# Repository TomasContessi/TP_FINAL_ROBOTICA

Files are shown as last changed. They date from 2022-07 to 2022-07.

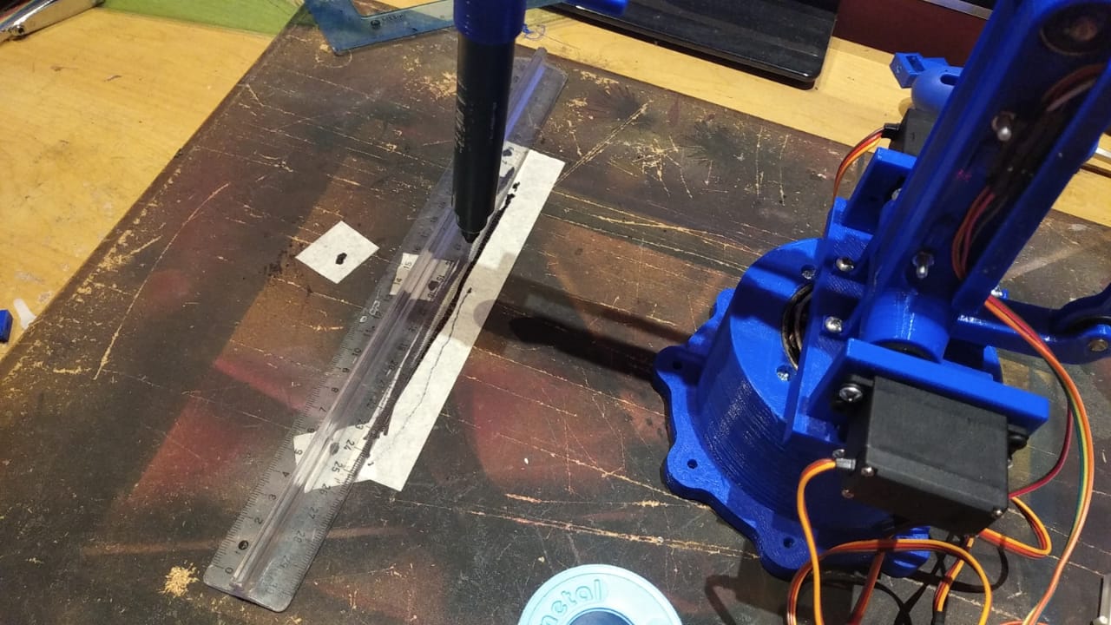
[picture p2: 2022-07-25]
robot irl/img/lineal.jpeg

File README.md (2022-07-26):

# TP FINAL ROBOTICA

Robot serie de 4 grados de libertad fabricado como tp final de la materia robotica.

precision

Especificaciones de diseño:

- Carga Maxima 400g
- Maxima extencion 250mm
- Repetitividad +-1mm
- Exactitud +-1mm
- Peso 1kg

Especificaciones del robot medidas en el prototipo final:

- Carga Maxima 200g
- Maxima extencion 250mm
- Repetitividad +-3mm
- Exactitud +-5mm
- Peso 934g

# Videos del robot

https://user-images.githubusercontent.com/55562600/180897072-30f60ed5-107a-4d38-ac05-319fecedbc43.mp4

https://user-images.githubusercontent.com/55562600/180897452-3dd9bf58-14a9-4827-a617-9365f39d61e9.mp4

https://user-images.githubusercontent.com/55562600/180897461-f654ef13-cb58-4b30-b609-2cc938e993c4.mp4

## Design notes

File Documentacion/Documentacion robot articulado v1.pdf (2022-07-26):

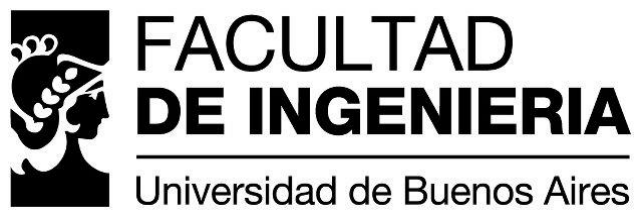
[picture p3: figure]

# Robótica

# Trabajo práctico FINAL-ROBOT

Nombre | Correo Electrónico
Tomas contessi | tcontessi@fi.uba.ar

# Índice:

- Descripción del proyecto.
- Especificaciones deseadas.
- Elección de componentes.
- Diseño de partes mecánicas.
- Simulación y obtención de modelos.
- Revisión de las especificaciones.
- Construcción del prototipo.
- Diseño e implementación del software.
- Pruebas sobre el prototipo y verificación de las especificaciones deseadas.
- Lista de componentes.
- Cosas por mejorar.

# Descripción del proyecto:

Se desea construir un modelo de robot serie de 4 grados de libertad capaz de realizar tareas del tipo pick and place.
Si bien existen modelos de robot y controladores de este estilo en internet, en este proyecto se diseñarán e implementarán tanto el hardware como el software necesario. Los modelos y el software resultantes serán subidos a un repositorio de GitHub para que cualquiera que lo desee pueda acceder a ellos y continuar el desarrollo o construir su prototipo.

Este proyecto utiliza Solid Works para el diseño de piezas mecánicas, simulación y obtención de características físicas, Arduino como plataforma de desarrollo para hacer de interfaz entre la pc y los motores y Python como lenguaje de programación para el controlador.

# Especificaciones deseadas:

Se desea que el prototipo de robot cumpla las siguientes especificaciones:

- Grados de libertad: 4.
- Máxima extensión: 250mm.
- Carga máxima en la brida a máxima extensión: 400g.
- Precisión: ±1mm.
- Repetitividad: ±1mm.
- Velocidad: 100º/seg.
- Peso del robot: 1kg.
- No se pondrán frenos mecánicos, solo los motores.

# Elección de componentes:

Para la construcción del modelo se eligieron los componentes siguiendo un criterio de precio/calidad y simplicidad, eligiéndose los siguientes:

- Motor para los ejes 1,2,3: servomotor Mg946r.
- Motor para el eje 4: servomotor Sg90.
- Placa de desarrollo: Arduino Nano.
- Rodamientos: rulemanes 6262RS
- Rodamiento eje 1: rulemán 30202JR o 30305JR (se utilizó este en el modelo fabricado).
- Material de fabricación de las partes: PLA.

# Diseño de las partes mecánicas:

El diseño del robot tomo inspiración de modelos como el IRB460 de ABB, ya que ese tipo de diseño maximiza la carga útil al poner los motores montados sobre el eje 1 y da la posibilidad de utilizar solo ejes giratorios, a diferencia de modelos como el SCARA. Aunque también tiene la contra de que es un diseño mecánicamente complejo, teniendo los motores de los ejes 2 y 3 montados de manera concéntrica y haciendo uso de un sistema de trapecios (en mi diseño se cambió por romboides) que garantiza que el eje de la brida siempre se mantenga paralelo al suelo.

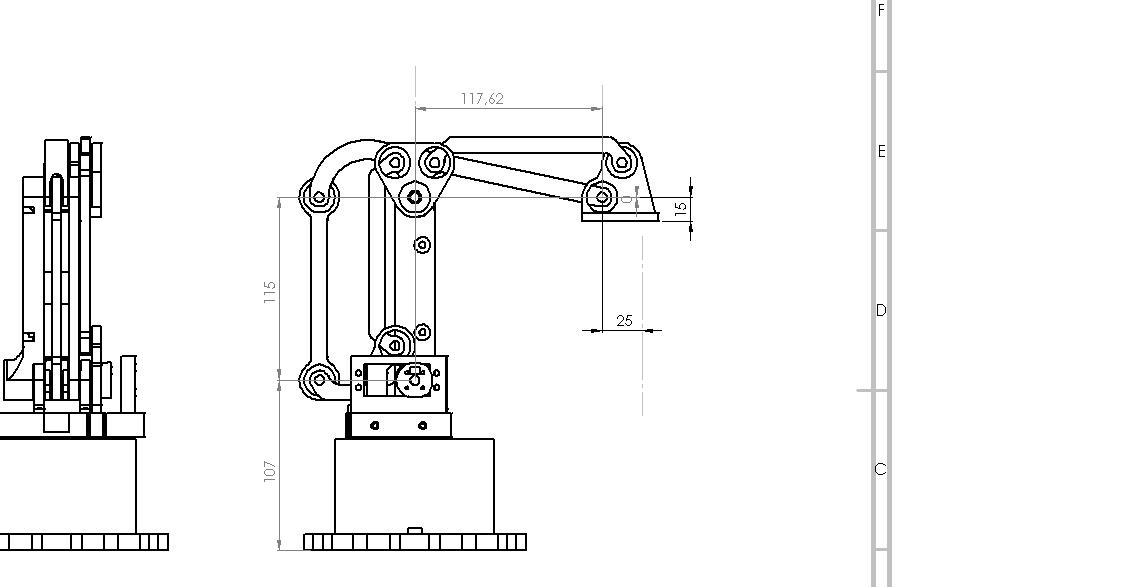
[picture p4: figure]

Como software de diseño se utilizó el Solid Works ya que permite diseñar piezas mecánicas de manera intuitiva y precisa.

Al diseñar el robot se buscaba que este sea capaz de plegarse sobre sí mismo, lo cual termino decidiendo gran parte de la forma de los segmentos 2 y 3.
El sistema de trapecios fue reemplazado por un sistema de romboides ya que resulta más simpe el diseño aunque se pierde algo de rango de movimiento.
Los ejes de los motores 2 y 3 se alinearon de manera concéntrica montando todo el sistema sobre rodamientos y haciendo el eje 2 del robot parte del eje del motor 3, de esta manera se mantiene la alineación de los motores y a su vez se transfiere la potencia a ambos ejes sin afectar al otro.

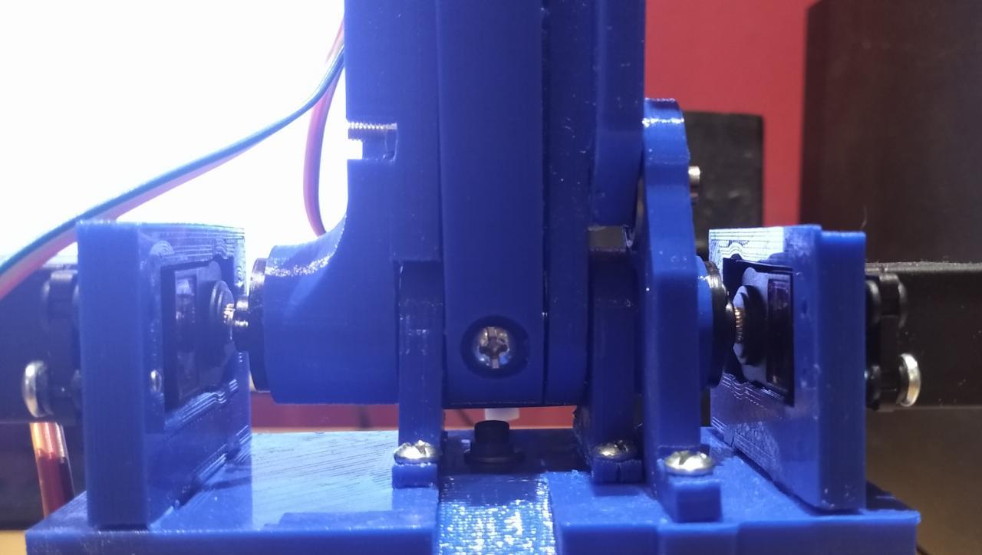
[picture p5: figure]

Además, como medida para mejorar la estabilidad, precisión y la resistencia del prototipo se decidió montar todo sobre rodamientos, incluido el eje 1, para el que se usó un rodamiento cónico.

# Simulación y obtención de modelos:

Al tener los diseños de las piezas terminados se procedió a realizar un montaje de estas usando la herramienta de ensamble del programa Solid Works, utilizando esta herramienta se simularon los movimientos del robot y se verifico que las piezas encastren y trabajen juntas como se esperaba y que el robot cumpliera las especificaciones de alcance máximo deseadas.

Utilizando el mismo programa se obtuvo la posición del centro de masa de las piezas del brazo y con el programa ultimakerCura, el cual es el que prepara el código para imprimir en 3D las partes se obtuvo el peso estimado que tendrían las partes ya impresas (con una densidad de relleno del 7%). Con esta información se calculó el torque que precisa el motor del eje 1 solo para levantar el robot (este motor es el que limita la capacidad de carga en este diseño).

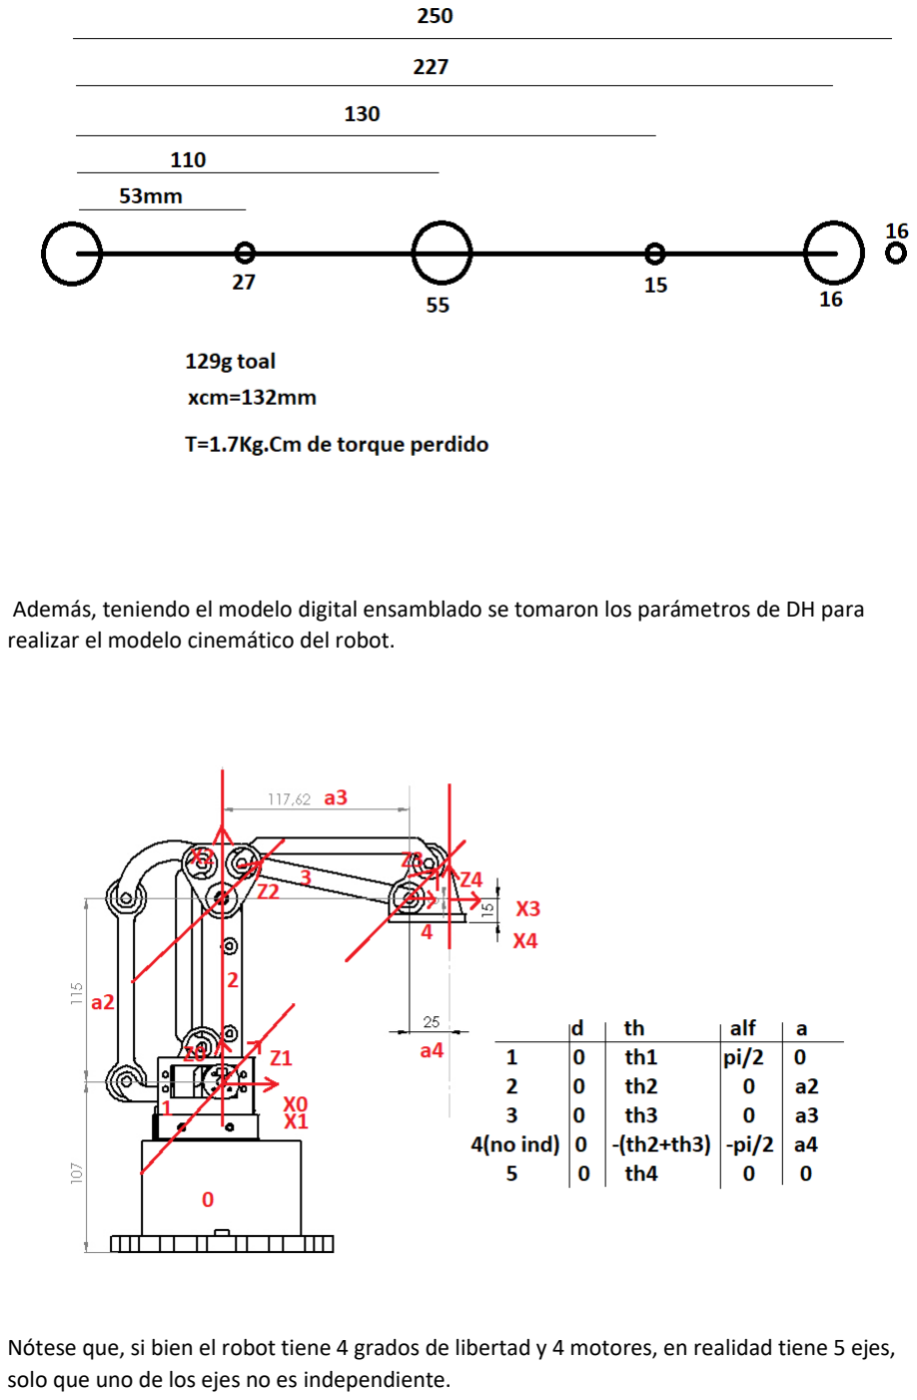
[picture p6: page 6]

Además, teniendo el modelo digital ensamblado se tomaron los parámetros de DH para realizar el modelo cinemático del robot.

Nótese que, si bien el robot tiene 4 grados de libertad y 4 motores, en realidad tiene 5 ejes, solo que uno de los ejes no es independiente.

Además, se imprimió una pieza de 10cm de largo para usarse en la medición del torque de los motores y se corroboro que a la tensión de trabajo estos tenían más de 12kg.cm de torque. (según su datasheet tienen entre 10 y 13kg.cm dependiendo de la tensión)

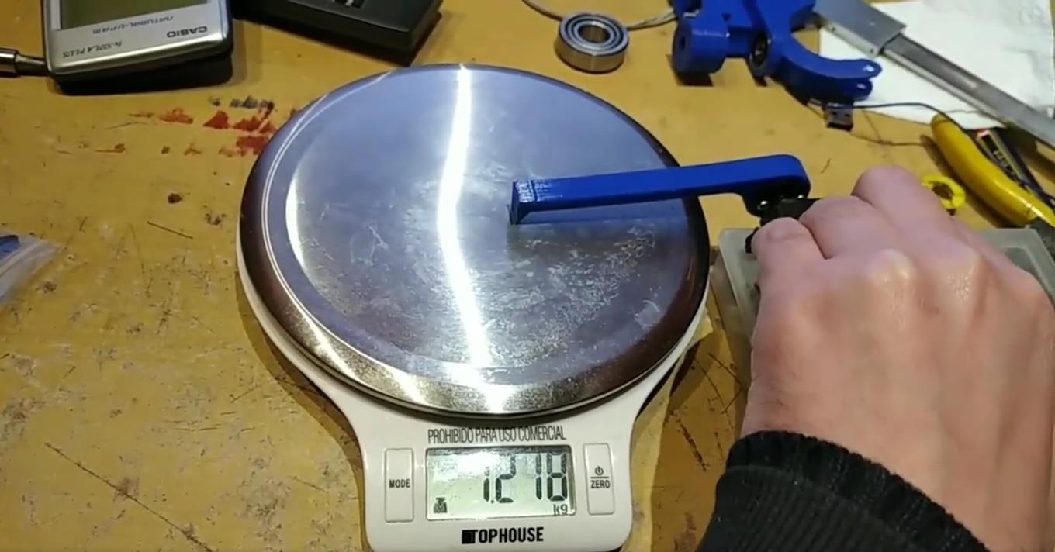
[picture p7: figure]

# Revisión de las especificaciones:

Una vez que se tuvo un modelo virtual del robot se procedió a ver si este diseño sería capaz de cumplir con las especificaciones planteadas.

- Del ensamble del modelo se verifico que el robot lograba alcanzar los 250mm en su máxima extensión.
- Al restar el torque necesario para mover el brazo del torque medido del motor se obtiene entonces un torque de 10.3kg.cm y dividiendo esto por 25cm obtenemos una capacidad de carga máxima de 412g.
- Según su datasheet los motores tienen una velocidad de 300º/seg en vacío, lo cual a priori cumpliría la especificación de velocidad, al menos en vacío.

# Construcción del prototipo:

El prototipo fue impreso en 3D en PLA, con una altura de capa de 0.15mm y una densidad de relleno del 7%.
Durante la construcción se decidió reemplazar el rodamiento cónico 30202JR por el 30305JR, ya que este último si bien es más caro, el radio interno permite acomodar mejor el eje del motor y al ser más grande proporciona un mejor apoyo a toda la estructura.
Para la colocación de los motores es recomendable hacer un programa que los haga apuntar a 90º y ponerlos de forma que los 90º queden a la mitad del movimiento de la articulación, igualmente el soft permite cargar como atributo el offset de la colocación de los motores, el cual es la diferencia entre la posición en la que fue colocado el motor y la posición a la que apunta el segmento del robot según los parámetros de DH.

Si bien se dejaron encastres para colocar tuercas en la plataforma del eje1, el robot fue diseñado para que no sean necesarias y los tornillos rosquen sobre el plástico facilitando el armado. Estos alojamientos para tuercas son por si se falsea la pieza, para que no haya que reemplazarla.

La forma correcta de ensamblar el modelo es:

1. Colocar todos los rodamientos en sus alojamientos y verificar que calcen derechos (entran a presión, posiblemente se requiera un tubo de 25mm para poner la pista interna del rulemán cónico en el eje1), también colocar y atornillar los acoples para los motores en sus respectivos encastres en los ejes, está diseñado para los acoles redondos de 22mm que vienen con los servos).
2. Colocar el motor del eje 1 y ensamblar la base:

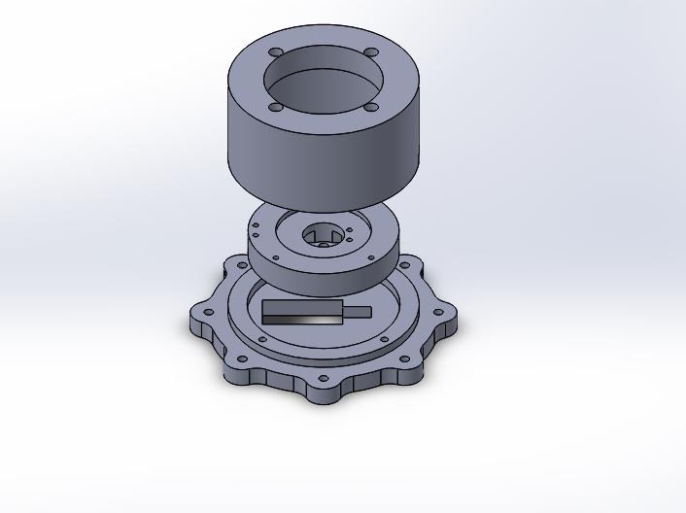
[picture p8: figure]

3. Ensamblar el segmento 4 del brazo que se pega con cualquier pegamento tipo la gotita o pegamentos para plásticos. Es recomendable colocar en este paso el motor del eje 4 ya que después será muy difícil con el eje 3 puesto:

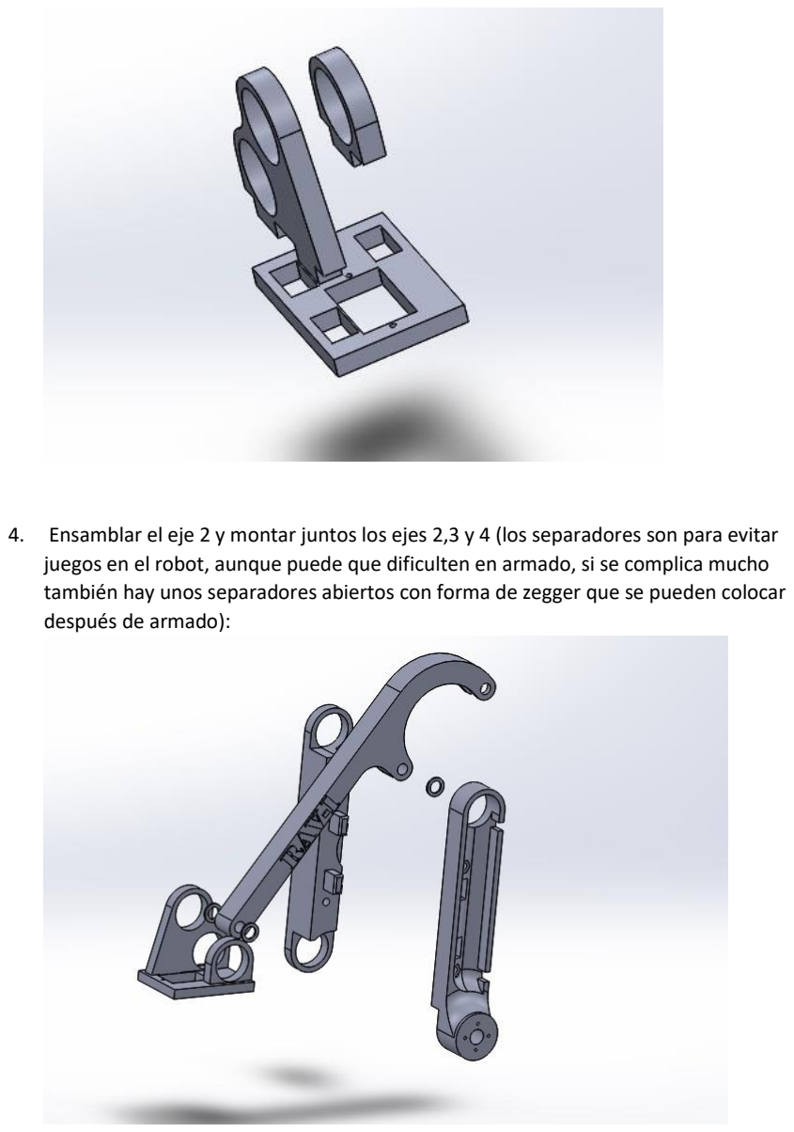
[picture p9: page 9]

4. Ensamblar el eje 2 y montar juntos los ejes 2,3 y 4 (los separadores son para evitar juegos en el robot, aunque puede que dificulten en armado, si se complica mucho también hay unos separadores abiertos con forma de zegger que se pueden colocar después de armado):

5. Colocar el eje en la pieza tractora del eje 3 y montar la articulación del eje 2, luego también montar la leva que transfiere el movimiento de la palanca al eje 3:

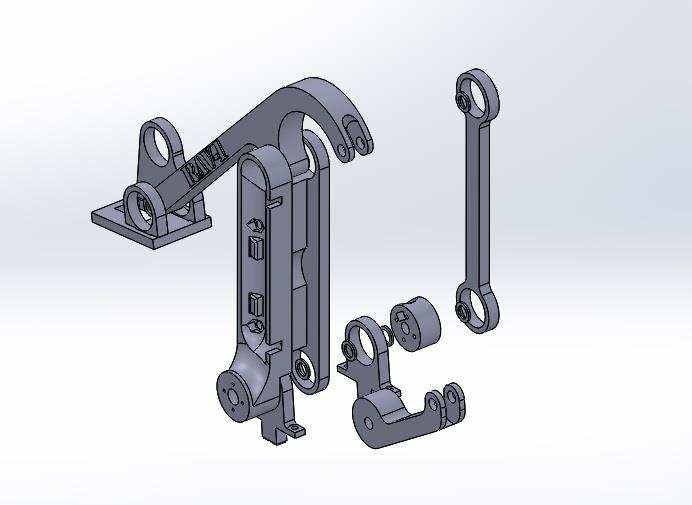
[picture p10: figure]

(nota, me acabo de dar cuenta que sería más fácil armar el segmento 2 en esta parte y apretar todo junto, pero estoy describiendo el orden el que lo pensé y arme yo)

6. Colocar el soporte de las paralelas en la plataforma, luego colocar el tractor con el centro del rulemán cónico en el hexágono y ensamblar el rulemán encastrando el tractor en el eje, asegurar toda la pieza atornillando con un tornillo de 40mm dese la plataforma hasta el motor:

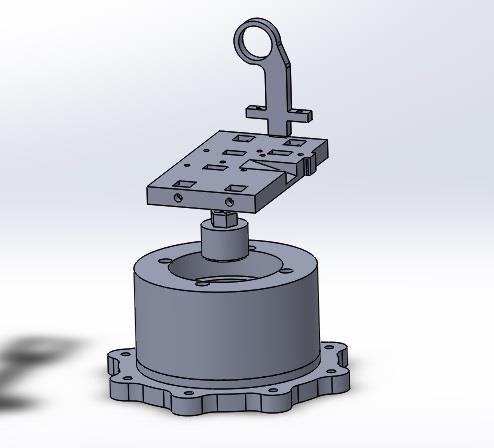
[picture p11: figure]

7. Luego atornillar los soportes del eje 2 a la plataforma, es posible que haya que aflojar un poco el soporte de las paralelas o forzarlo un poco porque entra muy justo. En este punto verificar que el eje 2 quede lo más paralelo con la plataforma posible (si

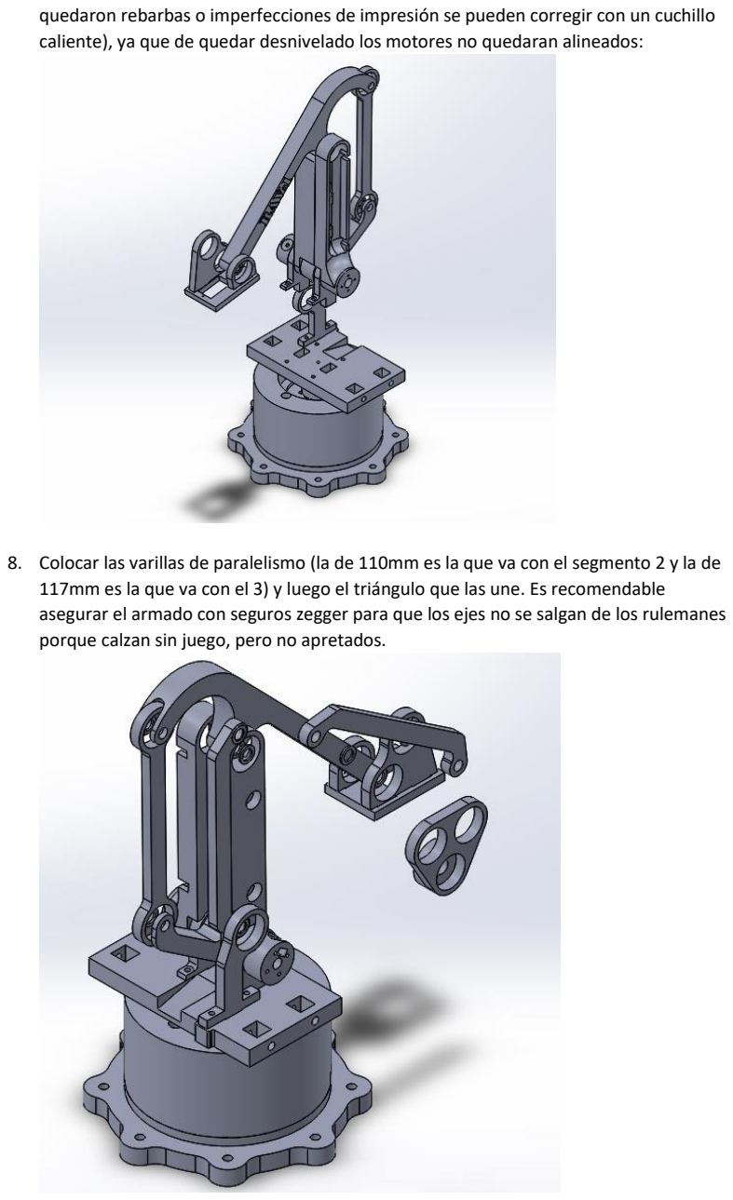
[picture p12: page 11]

quedaron rebarbas o imperfecciones de impresión se pueden corregir con un cuchillo caliente), ya que de quedar desnivelado los motores no quedaran alineados:

8. Colocar las varillas de paralelismo (la de 110mm es la que va con el segmento 2 y la de 117mm es la que va con el 3) y luego el triángulo que las une. Es recomendable asegurar el armado con seguros zegger para que los ejes no se salgan de los rulemanes porque calzan sin juego, pero no apretados.

9. Colocar los soportes de los motores sin atornillarlos, luego calzar los motores en sus acoples y sus soportes y atornillar todo en su lugar para completar el montaje:

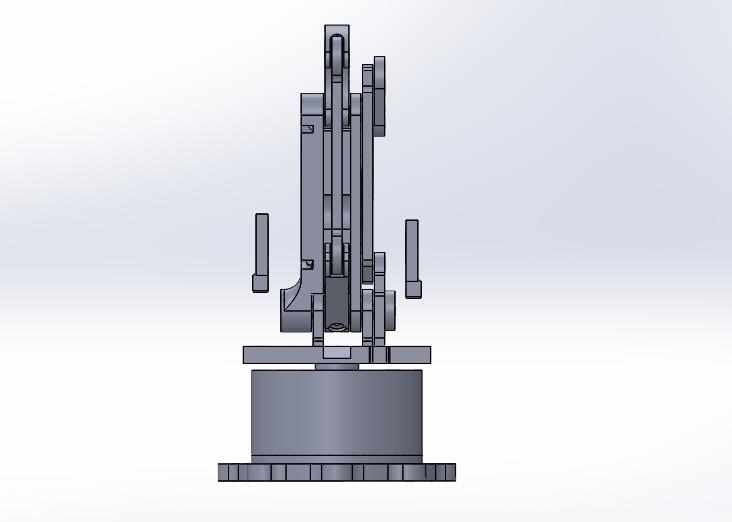
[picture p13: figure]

Con el robot ya terminado se puede probar de manera manual cargando en el Arduino el programa “joggin_manual_noPC”, el cual permite controlar los ejes con potenciómetros.

# Diseño e implementación del software:

Se decidió implementar el software de control en Python por su simplicidad de uso.
Al diseñar la interfaz con el usuario se buscaba que sea lo más similar a la de los programas para robots como el visto en clase, por lo que se intentó replicar el set de instrucciones.
Se implemento un módulo robot_t, el cual contiene la definición del objeto robot, este tiene las funciones de los movimientos joint y lineales, así como la cinemática directa e inversa del robot (como se usaron servos no se implementó un controlador como tal para los motores ya que este está embebido en el servo), el robot cuenta también con atributos para definir la herramienta y la transformación de la base a la terna de referencia del robot, también se puede activar el gripper o los motores con estos atributos y setear una pose de home.
En la parte del Arduino se buscó que fuera lo más simple posible, por lo que este solo recibe por medio del puerto USB una línea de comandos de la forma “<th1:th2:th3:th4:gripperState:motorsState>”, la procesa, ejecuta y envía un carácter de acknorage a la pc para que esta le envíe el siguiente comando.

Para programar una rutina en el robot solo se debe importar el módulo, crear el objeto robot, configurar el puerto en el que se conectó el USB (si se desea también se pueden configurar el home, la herramienta, etc.) y luego escribir un programa utilizando los comandos MoveL y MoveJ para ordenarle al robot que hacer y cambiando el estado del gripper si se desea activarlo o desactivarlo.
Los comandos de movimiento reciben una pose de la forma [X,Y,Z,th] y en el caso del movimiento lineal el tiempo que se desea que tarde el movimiento.
En el caso de los movimientos joint, como no se implementó aun un control de velocidad estos se ejecutan a máxima velocidad y es conveniente poner un delay entre comandos en el programa para darle tiempo al robot a completarlos.

Los movimientos lineales son procesados en tiempo real paso a paso del ciclo de control, por lo que es posible pararlos a la mitad de la ejecución si se cierra el programa (aún no se implementó un comando de stop presionando una tecla). Debido a que no es posible controlar la velocidad con la que se mueven los servos, estos movimientos se realizan sumando una serie de movimientos joint muy cortos

Si bien era posible y quizá más prolijo realizar todo el controlador en una raspberryPi en vez de usar una pc y un Arduino esta opción no se utilizó por motivos de costos.

El software implementado en Python utiliza los módulos pyserial y sympy

# Pruebas sobre el prototipo y verificación de las especificaciones deseadas:

- precisión y repetitividad:
Se probaron la precisión y la repetitividad del robot haciéndolo repetir 60 veces una secuencia de 4 movimientos en los cuales el robot tenía que marcar 4 puntos en el suelo con un fibron, luego se midió la dispersión de dichos puntos para corroborar la repetitividad y se midió la posición de los clústeres de puntos respecto de las posiciones deseadas para verificar la precisión.

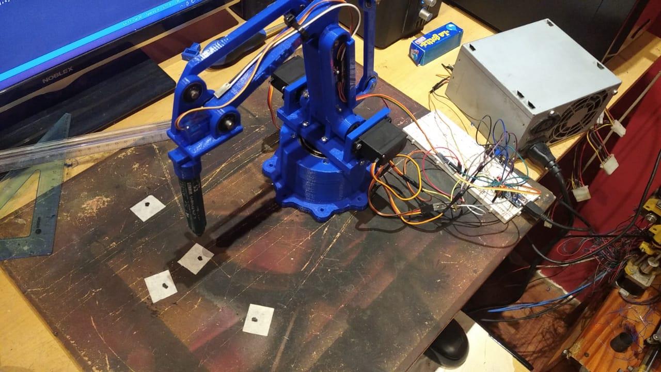
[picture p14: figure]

RESULTADO:

PRECISION: ± 5mm
REPETITIVIDAD: ± 3mm
- Linealidad:
La capacidad de realizar movimientos lineales se probó de manera similar, se hizo al robot trazar 20 líneas rectas y al finalizar se compararon dichas líneas con una regla para verificar que sean trazos rectos.

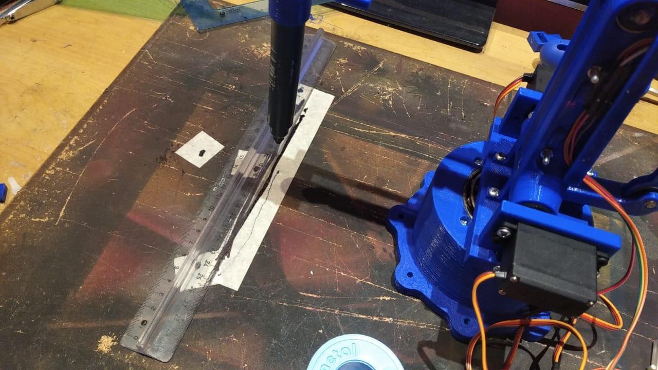
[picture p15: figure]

Debido a la precariedad del montaje del fibron la prueba no fue eficaz a la hora de cuantificar la linealidad, solo se pudo verificar que el robot es capaz de hacer movimientos “lineales” bastante consistentes, ya que todos los trazos en ambos sentidos quedaron superpuestos.

- Capacidad de carga:

Se realizaron pruebas haciendo al robot levantar cargas conocidas, se verifico que es capaz de levantar cargas hasta 260g, pero no llevarlas a la pose deseada. La máxima capacidad de carga con la que puede alcanzar una pose deseada es 200g

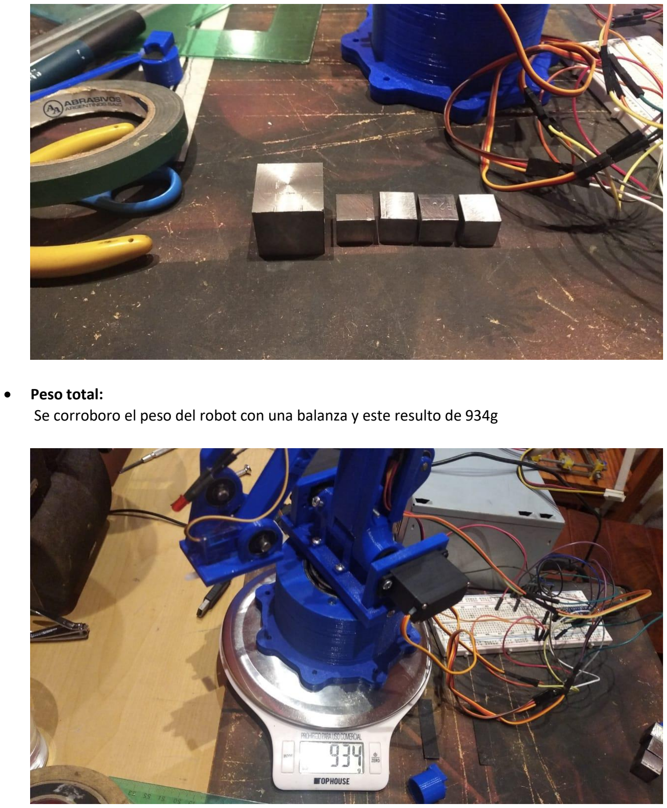
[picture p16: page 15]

- Peso total:
Se corroboro el peso del robot con una balanza y este resulto de 934g

# Lista de componentes:

- Rodamientos:
15 | 6262RS
1 | 30202JR o 30305JR
- Motores:
3 | MG946R
1 | SG90
- Interfaz:

1 Arduino Nano con cable USB (cualquier Arduino debería servir)

- Burlonería:
6 | tornillos de 3/2in con tuercas
18 | tornillos de 1/2in
6 | tornillos de 1in
1 | varilla rectificada de 6mm
8 | seguros zegger de 6mm
- Varios:
1 | Fuente 5V 5A
1 | Cap 22uf
1 | Cap .22pf
1 | Protoboard
n | Cables

# Cosas por mejorar:

En futuras versiones del modelo se debería:

1. Mejorar el diseño de la brida, ya que el eje del servomotor del eje 4 no es estable para montar herramientas.
2. Utilizar motores mas precisos y en los cuales se pueda controlar la velocidad con precisión, porque los servos tienen una resolución de 1º y un juego muerto también de 1º, lo cual genera un gran juego muerto en la herramienta.
3. Implementar el control de velocidad en los movimientos joint.
4. Montar la interfaz en una placa.
5. Solucionar el problema de que el brazo se mueve aleatoriamente al establecer la conexión serie.

6. Agregar feedback de información procedente de sensores en el robot.
7. Hacer los movimientos controlando la velocidad de los motores.
8. Es posible mejorar los servos sacándoles el controlador que traen y controlándolos uno mismo desde el programa, lo cual mejoraría en gran medida el funcionamiento general.

El código, los modelo y todo el material desarrollado para este trabajo pueden descargarse del repositorio:
https://github.com/TomasContessi/TP_FINAL_ROBOTICA.git

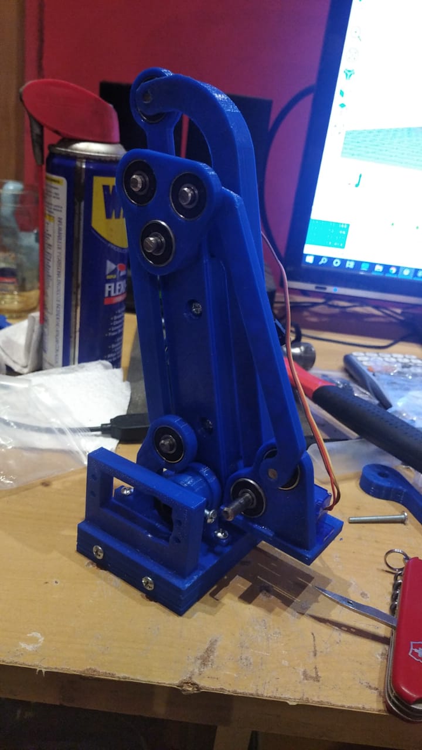
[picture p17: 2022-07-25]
robot irl/img/brazo.jpeg

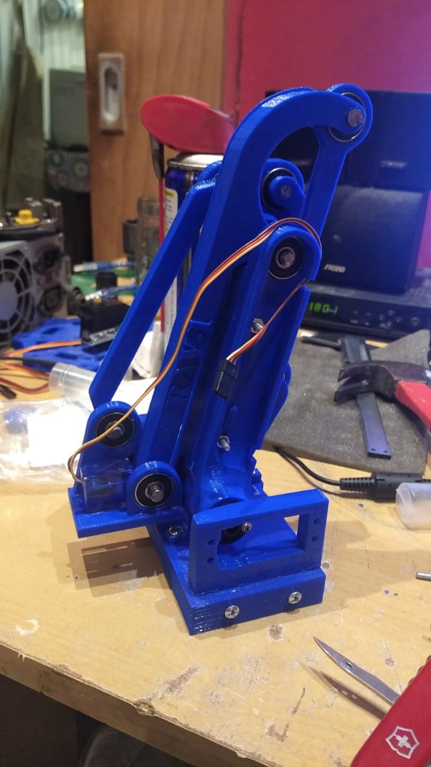
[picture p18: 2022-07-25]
robot irl/img/brazo2.jpeg

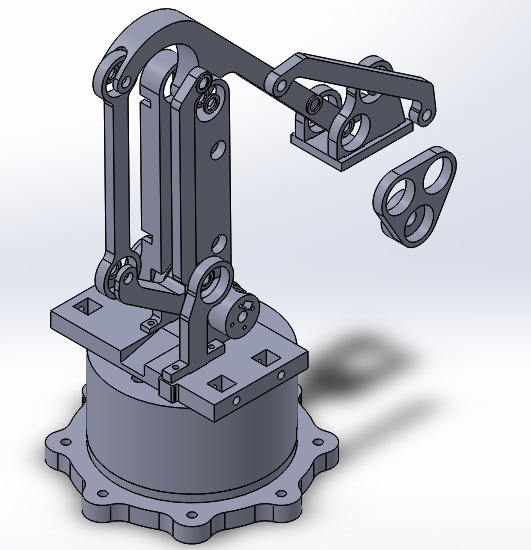
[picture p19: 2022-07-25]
planos/paralelas.jpg

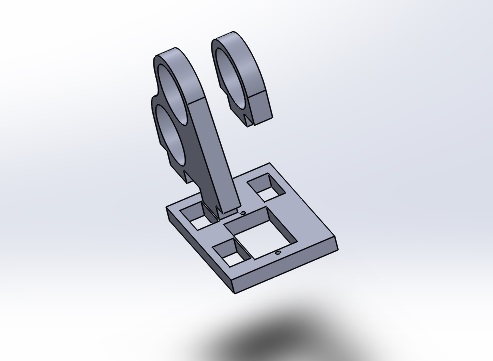
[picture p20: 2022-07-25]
planos/eje4.jpg

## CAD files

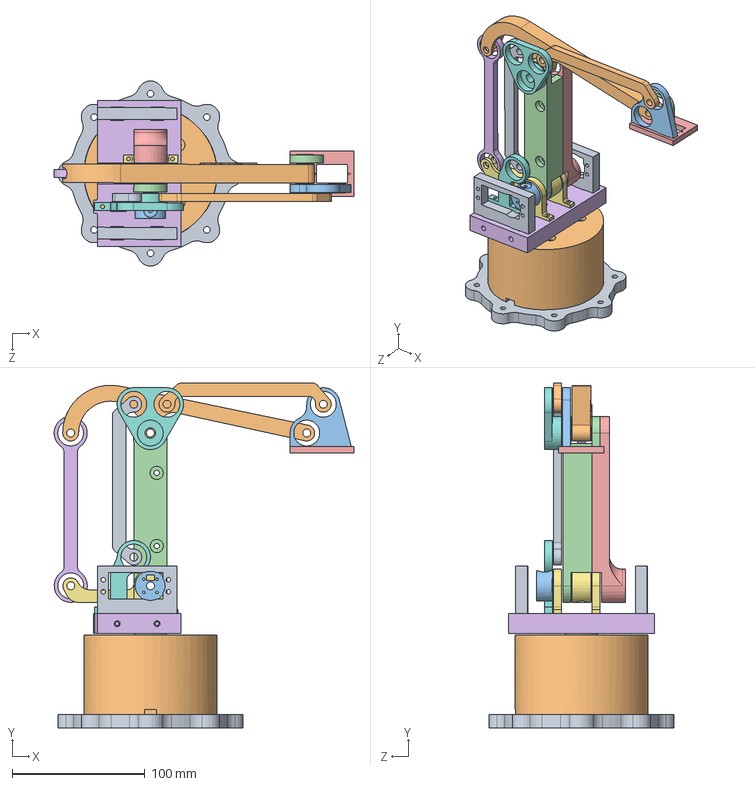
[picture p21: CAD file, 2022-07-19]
ensambles/Ensamble completo.SLDASM
225.7 x 259.7 x 139.3 mm
Base_A
Base_B
Base_C
30202JR
Eje_1_tractor
Eje_1_plataforma
Soporte_eje_2 x 2
Soporte_paralelas
Soporte_motor x 2
Eje_3
Eje_4_A
Eje_4_B
Eje_4_C
Leva_eje_3
Panalca_eje_3
Triangulo
Varilla_115mm
Varilla_117mm
eje_3_tractor
Eje_2_A
Eje_2_B

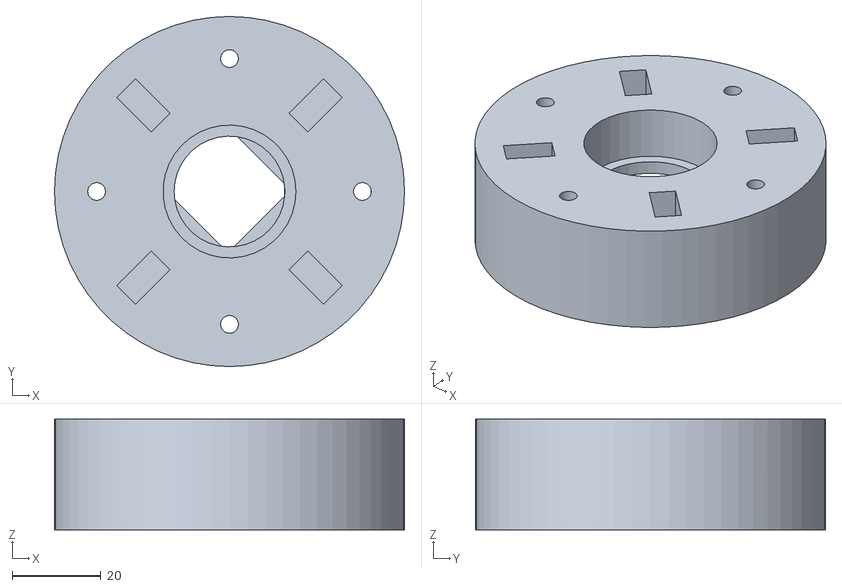
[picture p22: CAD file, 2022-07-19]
imprimibles/base/Base_C.STL
79.0 x 79.0 x 25.0

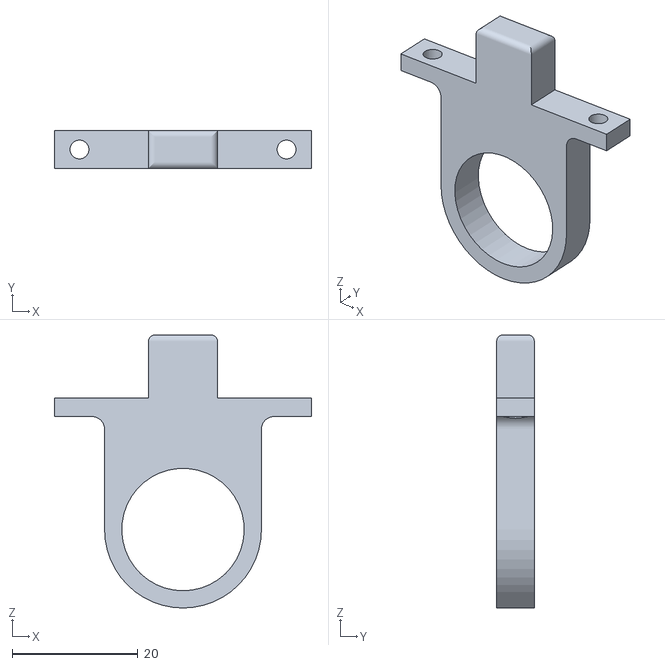
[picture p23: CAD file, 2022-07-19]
imprimibles/eje_1/Soporte_eje_2.STL
41.0 x 6.00 x 43.5

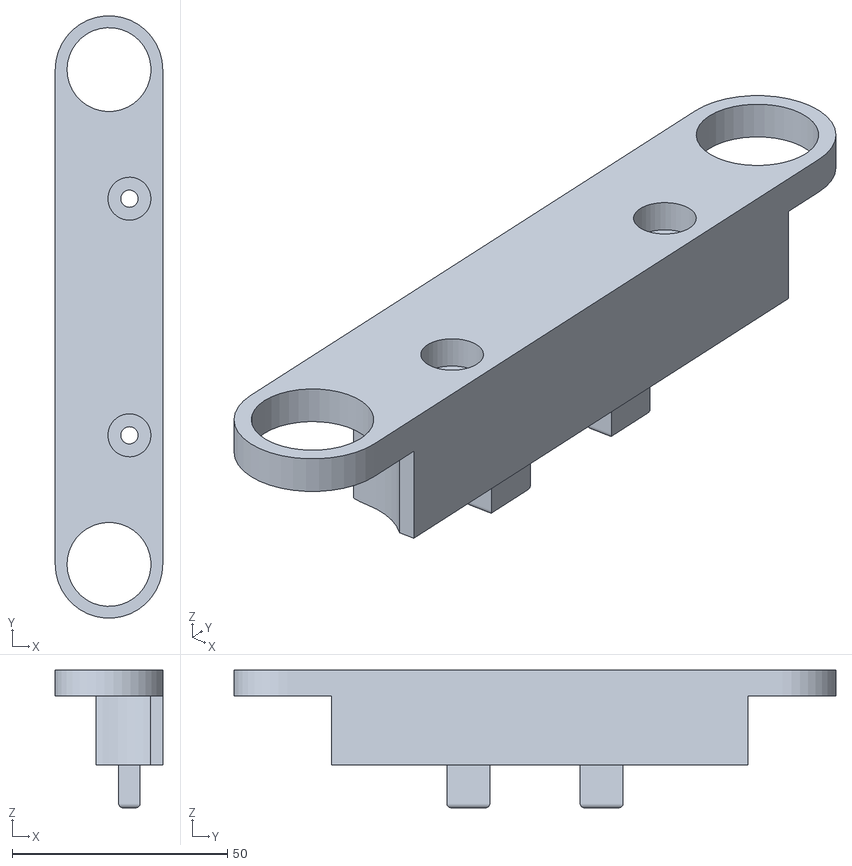
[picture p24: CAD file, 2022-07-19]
imprimibles/eje_2/Eje_2_A.STL
25.0 x 139.9 x 32.0

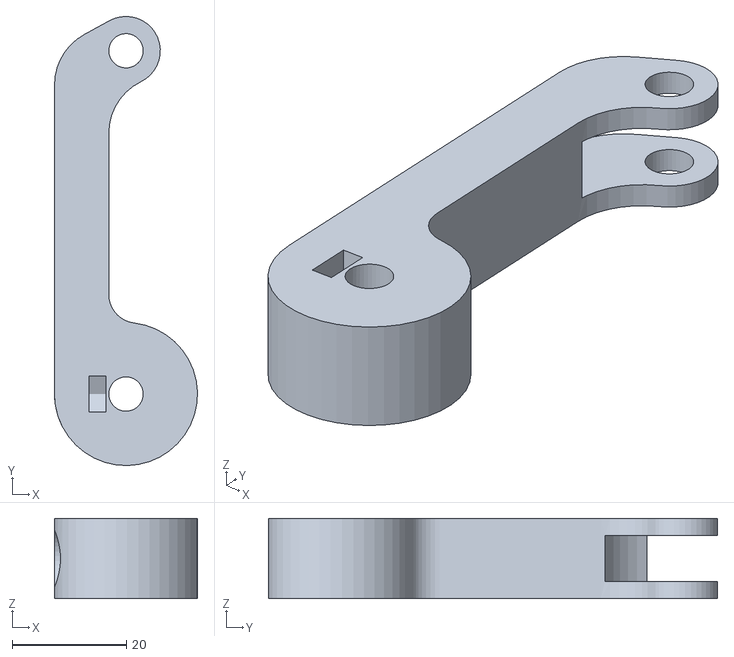
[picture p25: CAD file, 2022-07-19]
imprimibles/eje_3/Panalca_eje_3.STL
25.0 x 78.5 x 14.0

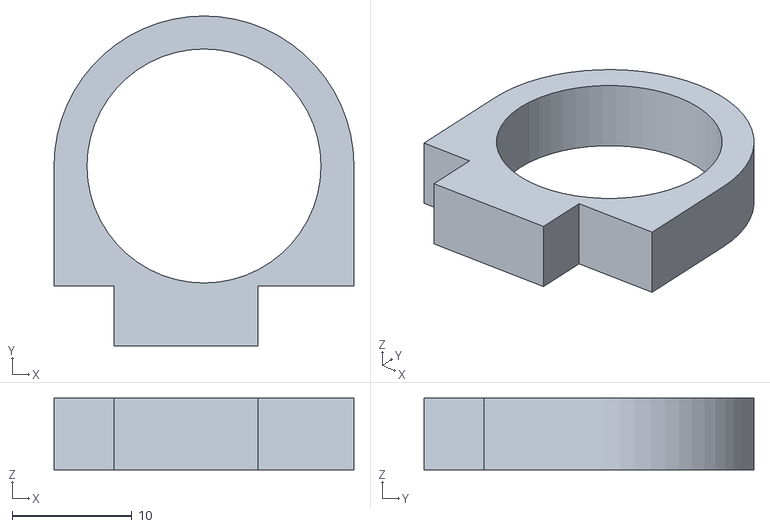
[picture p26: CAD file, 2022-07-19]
imprimibles/eje_4/Eje_4_B.STL
25.0 x 27.5 x 6.00

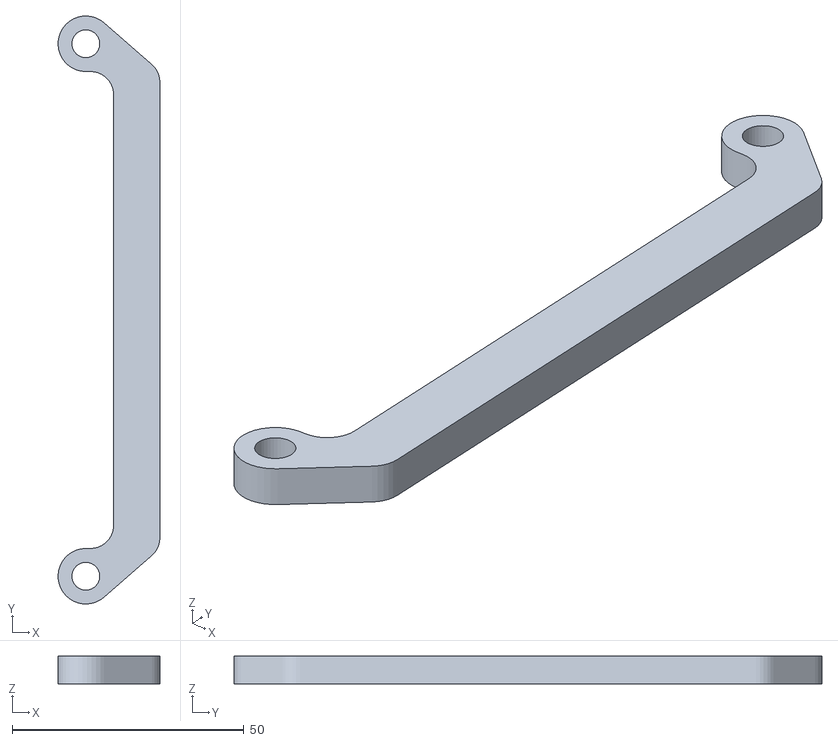
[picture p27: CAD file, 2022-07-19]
imprimibles/paralelas/Varilla_115mm.STL
22.0 x 127.0 x 6.00

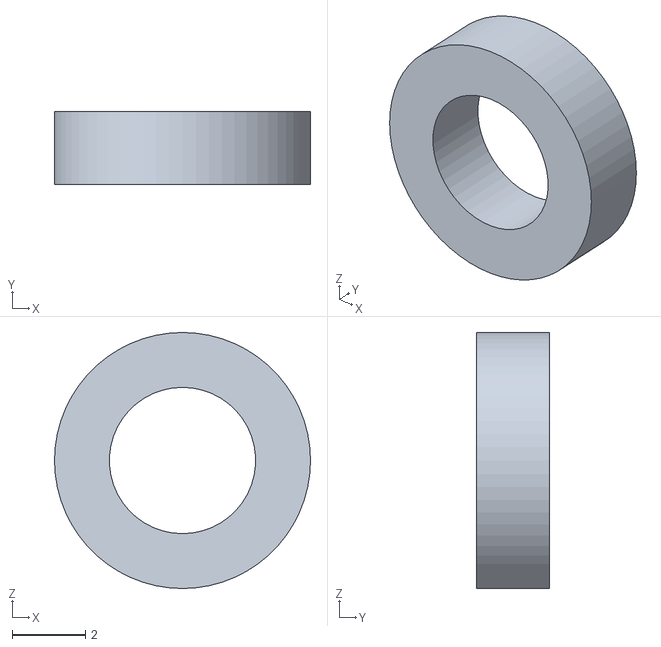
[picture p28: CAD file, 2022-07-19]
imprimibles/separador 2mm.STL
7.00 x 2.00 x 7.00

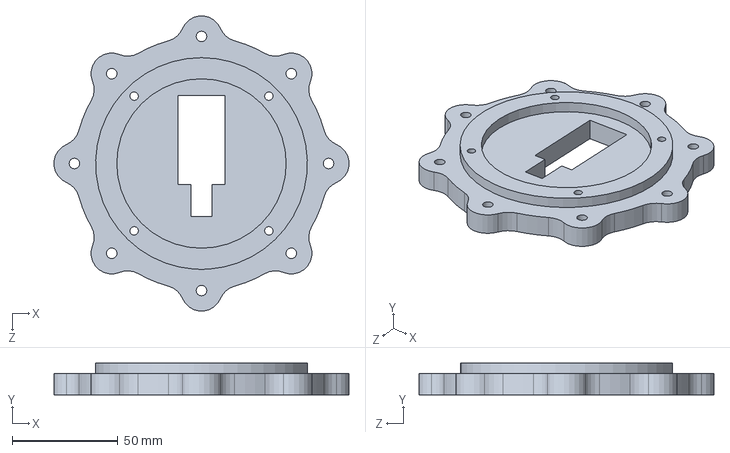
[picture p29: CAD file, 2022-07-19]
piezas/Base_B_V2.SLDPRT
139.3 x 15.0 x 139.3 mm

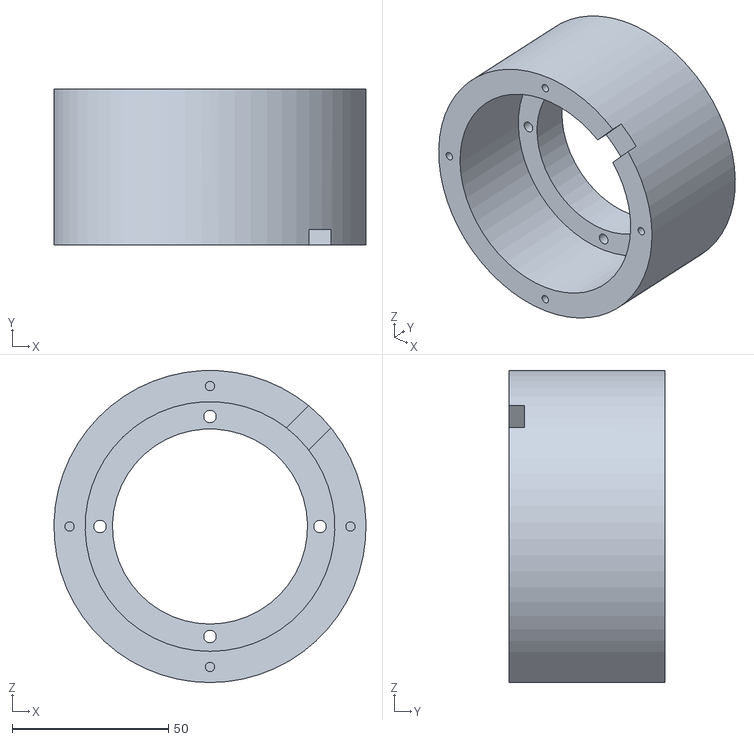
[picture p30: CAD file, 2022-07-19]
imprimibles/base/Base_A_V2.STL
100.0 x 50.0 x 100.0

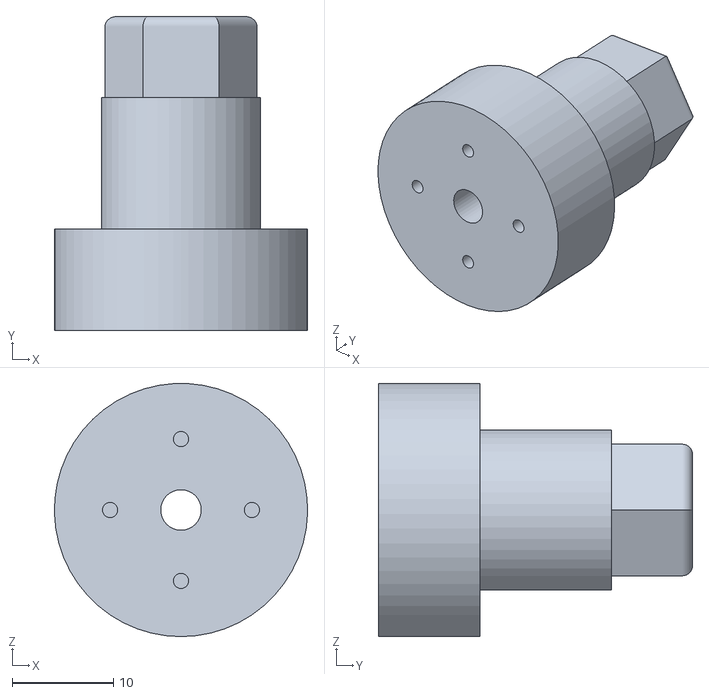
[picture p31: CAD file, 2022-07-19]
imprimibles/eje_1/Eje_1_tractor.STL
25.0 x 31.0 x 25.0

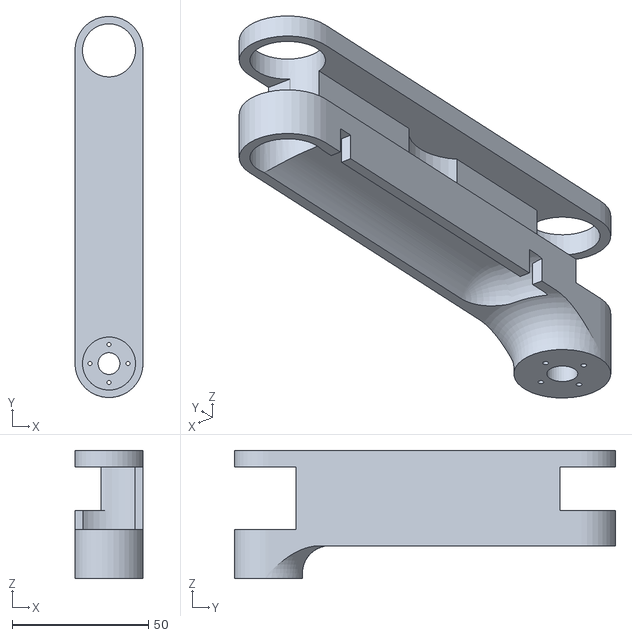
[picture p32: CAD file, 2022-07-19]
imprimibles/eje_2/Eje_2.STL
25.0 x 139.9 x 47.0

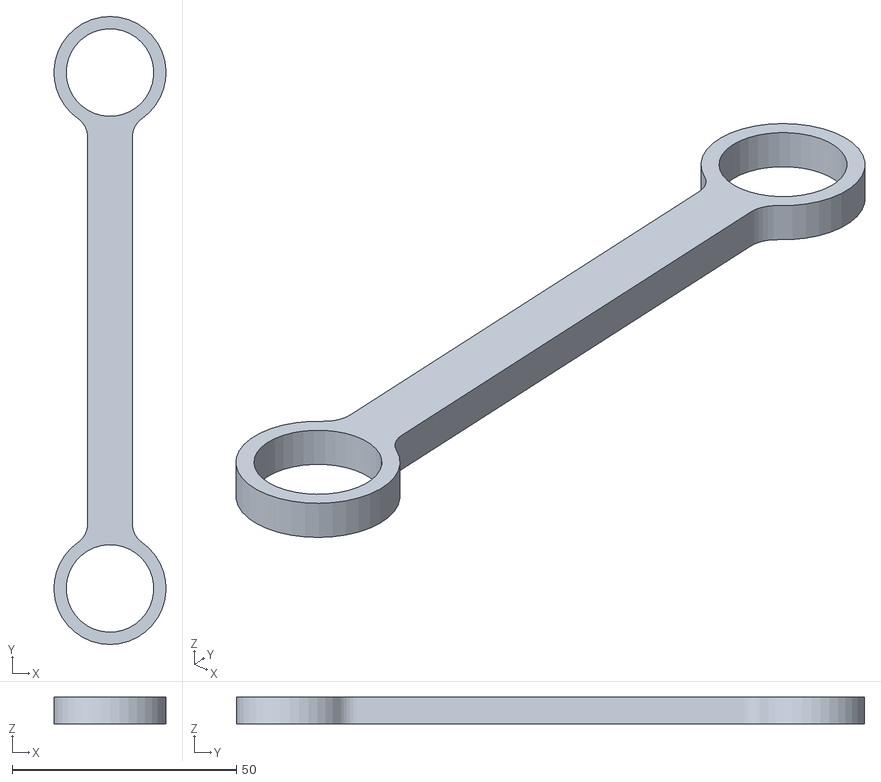
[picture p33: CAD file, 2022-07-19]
imprimibles/eje_3/Leva_eje_3.STL
25.0 x 140.0 x 6.00

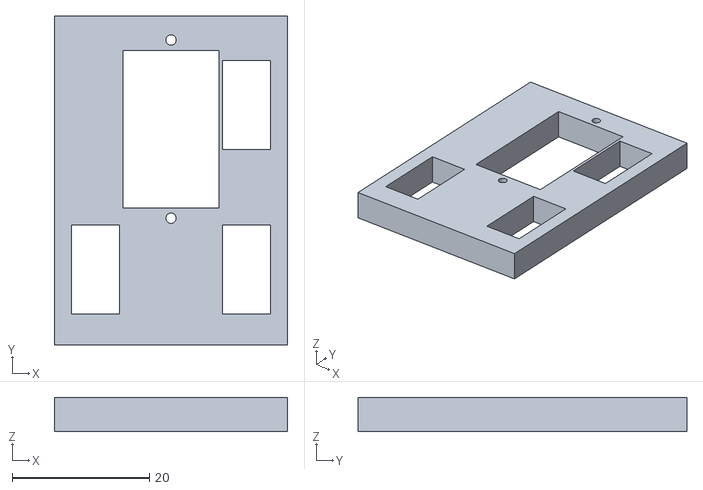
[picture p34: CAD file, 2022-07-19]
imprimibles/eje_4/Eje_4_C.STL
34.0 x 48.0 x 5.00

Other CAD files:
imprimibles/medidor_de_torque.STL
imprimibles/paralelas/Triangulo.STL
piezas/Eje_2_B.SLDPRT
imprimibles/base/Base_C_V2.STL
imprimibles/base/Base_A.STL
imprimibles/base/Base_B.STL
imprimibles/base/Base_B_V2.STL
imprimibles/base/separador_V1-V2.STL
imprimibles/eje_1/Eje_1_plataforma.STL
imprimibles/eje_1/Eje_1_plataforma_V2.STL
imprimibles/eje_1/Eje_1_tractor_V2.STL
imprimibles/eje_1/Soporte_motor.STL
imprimibles/eje_1/Soporte_motor_d.STL
imprimibles/eje_1/Soporte_motor_i.STL
imprimibles/eje_1/Soporte_paralelas.STL
imprimibles/eje_2/Eje_2_A_extra_alcance.STL
imprimibles/eje_2/Eje_2_B.STL
imprimibles/eje_2/Eje_2_B_extra_alcance.STL
imprimibles/eje_3/Eje_3.STL
imprimibles/eje_3/eje_3_tractor.STL
imprimibles/eje_4/Eje_4_A.STL
imprimibles/paralelas/Varilla_117mm.STL
imprimibles/separador 5mm.STL
imprimibles/separador_6-10x1 abierta.STL
imprimibles/separador_6-10x1.STL
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

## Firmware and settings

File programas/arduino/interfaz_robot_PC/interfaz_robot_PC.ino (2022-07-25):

#include <Servo.h>

Servo eje1;  // crea el objeto servo
Servo eje2;  // crea el objeto servo
Servo eje3;  // crea el objeto servo
Servo eje4;  // crea el objeto servo

int pwm1 = 2;        // uso la pata D2 para enviar el PWM al servo 1
int pwm2 = 3;        // uso la pata D3 para enviar el PWM al servo 2
int pwm3 = 4;        // uso la pata D4 para enviar el PWM al servo 3
int pwm4 = 5;        // uso la pata D5 para enviar el PWM al servo 4
int gripper_out = 6; // uso la pata D6 para el gripper

const int pinLED = 13;
int Q[] = {90,140,40,90};
int gripper = 0;
int motors = 0;
// home <90:140:40:0>
int QlimPos[] = {180,152,40,180,0};//Q3 tambien tiene de limite Q2-algo porque como estan invertidos es complicado sacar la relacion Q2=70->Q3=45
int QlimNeg[] = {0,54,150,0,0};

const byte buffSize = 40;
char inputBuffer[buffSize];
const char startMarker = '<';
const char endMarker = '>';
byte bytesRecvd = 0;
boolean readInProgress = false;
boolean newDataFromPC = false;

float inicio =0;
float fin = 0;

void setup(){
  eje1.attach(pwm1);  // vinculo los servos
  eje2.attach(pwm2);
  eje3.attach(pwm3);
  eje4.attach(pwm4);

   
  Serial.begin(115200);
  Serial.write(".");
  pinMode(pinLED, OUTPUT);
  pinMode(gripper_out, OUTPUT);
  }


void loop(){
  inicio=millis();                              // establesco un Ts de 20ms
  fin= inicio+20;

  
  
  if (Serial.available()>0) 
  {
    digitalWrite(pinLED, HIGH);
    SerialEvent();
    digitalWrite(pinLED, LOW);
    Serial.write(".");
    // actualizo los servos 
    if (motors == 1)
    {
      eje1.write(Q[1]); 
      eje2.write(Q[2]); 
      eje3.write(Q[3]); 
      eje4.write(Q[4]);
    }
  }


  digitalWrite(gripper_out, gripper);
  while (fin > millis())  {}
}

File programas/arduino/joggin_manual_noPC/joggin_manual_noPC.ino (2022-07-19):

#include <Servo.h>

Servo eje1;  // crea el objeto servo
Servo eje2;  // crea el objeto servo
Servo eje3;  // crea el objeto servo
Servo eje4;  // crea el objeto servo

// eje 1
int pot1 = 15;       // uso la pata A1 para leer la tension del pote      
int pwm1 = 2;        // uso la pata D2 para enviar el PWM
float pos1 = 0;      // posicion del servo
float e1lp=0;
float e1lp2=0;
float e1lp3=0;
float e1lp4=0;

// eje 2
int pot2 = 16;       // uso la pata A2 para leer la tension del pote      
int pwm2 = 3;        // uso la pata D3 para enviar el PWM
float pos2 = 0;      // posicion del servo
float e2lp=0;
float e2lp2=0;
float e2lp3=0;
float e2lp4=0;

// eje 3
int pot3 = 17;       // uso la pata A3 para leer la tension del pote      
int pwm3 = 4;        // uso la pata D4 para enviar el PWM
float pos3 = 0;      // posicion del servo
float e3lp=0;
float e3lp2=0;
float e3lp3=0;
float e3lp4=0;

// eje 4
int pot4 = 18;       // uso la pata A4 para leer la tension del pote      
int pwm4 = 5;        // uso la pata D5 para enviar el PWM
float pos4 = 0;      // posicion del servo
float e4lp=0;
float e4lp2=0;
float e4lp3=0;
float e4lp4=0;

float inicio =0;
float fin = 0;
float r = 0;

void setup() {
   eje1.attach(pwm1);  // vincula los servos
   eje2.attach(pwm2);
   eje3.attach(pwm3);
   eje4.attach(pwm4);
   
   Serial.begin(115200);
}

void loop() {
      inicio=millis();                              // establesco un Ts de 10ms
      fin= inicio+1;

      // leo el pote del eje 1
      pos1 = analogRead(pot1)/5;
      pos1 = (pos1+e1lp+e1lp2+e1lp3+e1lp4)/5;
      e1lp4=e1lp3;
      e1lp3=e1lp2;
      e1lp2=e1lp;
      e1lp=pos1;

      // leo el pote del eje 2
      pos2 = analogRead(pot2)/5;
      pos2 = (pos2+e2lp+e2lp2+e2lp3+e2lp4)/5;
      e2lp4=e2lp3;
      e2lp3=e2lp2;
      e2lp2=e2lp;
      e2lp=pos2;

      // leo el pote del eje 3
      pos3 = analogRead(pot3)/5;
      pos3 = (pos3+e3lp+e3lp2+e3lp3+e3lp4)/5;
      e3lp4=e3lp3;
      e3lp3=e3lp2;
      e3lp2=e3lp;
      e3lp=pos3;

      // leo el pote del eje 4
      pos4 = analogRead(pot4)/5;
      pos4 = (pos4+e4lp+e4lp2+e4lp3+e4lp4)/5;
      e4lp4=e4lp3;
      e4lp3=e4lp2;
      e4lp2=e4lp;
      e4lp=pos4;

      // envio la nformacion de las mediciones por si se quiere ver algo para debuggear
      Serial.println(pos1);
      Serial.println(pos2);
      Serial.println(pos3);
      Serial.println(pos4);
      


      // actualizo los servos
      eje1.write(pos1); 
      eje2.write(pos2); 
      eje3.write(pos3); 
      eje4.write(pos4); 
      
      while (fin > millis())  {}             
}

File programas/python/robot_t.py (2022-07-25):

from math import degrees
from numbers import Real
from sympy import *
import sympy
from A_a2b import P2A, A_a2b
import serial,time
from empaquetador import empaquetar

class robot:
    _pos = [0,0,0,0] #pose del robot actual, no tocar
    _d = [0,0,0,0,0] #parametro de dh d
    _alfa = [-pi/2,0,0,pi/2,0] #parametro de dh alfa 
    _a = [0,115,117,25,0] #parametro de dh a
    _vth_max = (5/3)*pi
    _home = [50,0,0,0] #home del robot, tocar con cuidado

    Ts = 20*10**(-3) #sample time del ciclo de control, si se modifica modificar tambien en el arduino
    offsets_motores = [95,50,90,85] #cuan torcidos pusiste los motores, con esto se ajusta para calibrar los angulos
    theta = [0,0,0,0] #parametro de dh theta, que ademas es la posicion de los motores
    A04 = eye(4) #transformacion que representa la pose actual del robot, tocar con cuidadoy de preferencia no tocar
    A_base = eye(4) #transformacion que representa la base del robot, asi toma el 0 en el cruce entre los ejes 1 y 2
    A_herr = eye(4) #transformcacion que representa la herramienta
    gripper = 0 #estado del gripper, 1 andando, 0 apagado
    motors = 0 #estado de los motores, 1 andando, 0 apagados
    puerto = 'COM5' # esto va a cambiar segun donde se conecte y hasta ahora no se como hacer para autodetectarlo
    brate = 115200 #baudrate, no tocar o si se toca cambiar tambien del arduino
#-------------------------------------------------------------------------------------------------------

#-------------------------------------------------------------------------------------------------------
    # Metodo que me calcula la cinematica directa del robot con los Q pasados por argumento
    # me devuelve la transformacion entre la base del robot y la herramienta, pero tambien guarda el A04
    # Q0 theta_1
    # Q1 theta_2
    # Q2 theta_3
    # Q3 theta_4
    def dir_cinematics(self,Q):   

        A = eye(4) #inicializo A como la matriz de rototranslacion nula alias identidad

        A[0,0] = -sin(Q[0])*sin(Q[3]) + cos(Q[0])*cos(Q[3])
        A[0,1] = -sin(Q[0])*cos(Q[3]) - cos(Q[0])*sin(Q[3])
        A[0,2] = 0
        A[0,3] = (self._a[1]*cos(Q[1]) + self._a[2]*cos(Q[1]+Q[2]) + self._a[3])*cos(Q[0])

        A[1,0] =  sin(Q[0])*cos(Q[3]) + cos(Q[0])*sin(Q[3])
        A[1,1] = -sin(Q[0])*sin(Q[3]) + cos(Q[0])*cos(Q[3])
        A[1,2] = 0
        A[1,3] = (self._a[1]*cos(Q[1]) + self._a[2]*cos(Q[1]+Q[2]) + self._a[3])*sin(Q[0])

        A[2,3] = -self._a[1]*sin(Q[1]) - self._a[2]*sin(Q[1]+Q[2])

        #A = sympy.simplify(A)
        return self.A_base * A * self.A_herr

#-------------------------------------------------------------------------------------------------------
# Este metodo me devuelve la matriz A04 expresada en funcion de los th
    def A04sym(self):
        A04_sym = eye(4)
        Q = symbols('th1,th2,th3,thni,th4')

        for  i in  range(0,5,1):
            A04_sym = A04_sym * A_a2b(self._d[i],Q[i],self._alfa[i],self._a[i])
        
        A04_sym = sympy.simplify( A04_sym )
        A04_sym = Subs(A04_sym,Q[3],-(Q[1]+Q[2]))
        return sympy.simplify( A04_sym )
#-------------------------------------------------------------------------------------------------------
    # Metodo que me calcula la cinematica inversa del robot con la Abase-brida (Abb) pasado por argumento
    # me devuelve las posiciones de las articulaciones del robot, este robot por su mecanica tiene siempre
    # solo una configuracion valida (brazo hacia arriba) asi que no es necesario pasarle un vector de 
    # configuracion, pero se lo voy a agregar para generalizar el modelo, cfg=1 es brazo hacia arriba,
    # cfg=-1 es brazo hacia abajo
    # Q0 theta_1
    # Q1 theta_2
    # Q2 theta_3
    # Q3 theta_4
    def inv_cinematics_c(self,Abb,cfg):
        A = self.A_base.inv() * Abb * self.A_herr.inv()
        th = [0,0,0,0]

        th[0] = atan2(A[1,3],cfg*A[0,3]) # calculo th 0
    
        s1=sin(th[0])
        
        c1=cos(th[0])

        s4 = A[1,0]*c1 - A[0,0]*s1 

        if c1 == 0: # uso la expresion que no se rompa por la singularidad de la division
            b = A[1,3]/s1 - self._a[3]
            c4 = -(A[0,1] + s4*c1)/s1
        else:
            b = A[0,3]/c1 - self._a[3]
            c4 = (A[0,0] + s4*s1)/c1

        # calculo th 4     
        th[3] = atan2(s4,c4) 

        c3 = ((b)**2 + A[2,3]**2 - (self._a[1]**2 + self._a[2]**2))/(2*self._a[1]*self._a[2]) # ahora calculo th3
        s3 = sqrt(1-c3**2)
        th[2] = atan2(s3,c3)
        

        # por ultimo calculo th2

        s2=(self._a[2]*(-A[2,3]*c3-b*s3)-self._a[1]*A[2,3])/(b**2 + A[2,3]**2)
        c2=(self._a[2]*(-A[2,3]*s3+b*c3)+self._a[1]*b)/(b**2 + A[2,3]**2)

        th[1] = atan2(s2,c2)

        return th
#-------------------------------------------------------------------------------------------------------
# el mismo metodo pero para no tener que poner siempre el cfg que no se necesita 
# (el brazo siemre mira arriba)
    def inv_cinematics(self,Abb):
        return self.inv_cinematics_c(Abb,1)
#-------------------------------------------------------------------------------------------------------
# metodo que inicia la posicion del robot y lo manda a home, no se por que pero cuando se establece la coneccion
# algo raro le pasa al arduino y el motor se mueve para cualquier lado o en el mejor de los casos apaga los motores
    def inicar(self):
        self.A04 = P2A (self._home)
        self._pos = self._home
        self.theta = self.inv_cinematics(self.A04)
        self.arduino = serial.Serial(self.puerto,self.brate)
        self.arduino.flushInput()
        self.arduino.flushOutput()
        time.sleep(0.7)
        self.motors = 1
        self.homeJ()

        
#-------------------------------------------------------------------------------------------------------
# metodo que manda al robot a hacer un home
    def homeJ(self):
        self.moveJ(self._home)
#-------------------------------------------------------------------------------------------------------
# metodo que hace al robot hacer un movimiento joint entre su pose actual y la pose deseada
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

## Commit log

2022-07-19 migrando los archivos
    migrando los archivos desde la pc
    [Base_A.STL, Base_A_V2.STL, Base_B.STL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]
2022-07-19 migrando los archivos
    [30202JR.SLDPRT, Base_A.SLDPRT, Base_A_V2.SLDPRT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]
2022-07-25 -codigos de demo
    [Ensamble_completo_V2.SLDASM]
2022-07-25 agregado de demo de cubitos
2022-07-26 agregado lo de controlar los servos
    se agrego en el to do lo de desarmar los servos y controlarlos uno mismo
